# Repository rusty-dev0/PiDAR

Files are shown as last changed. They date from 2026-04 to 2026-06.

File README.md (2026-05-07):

# PiDAR
An autonomous robot that builds a real-time 2D map of an unknown room using LiDAR and SLAM, with live visualization and path tracking, and even a custom development board for all of its locomotive needs!

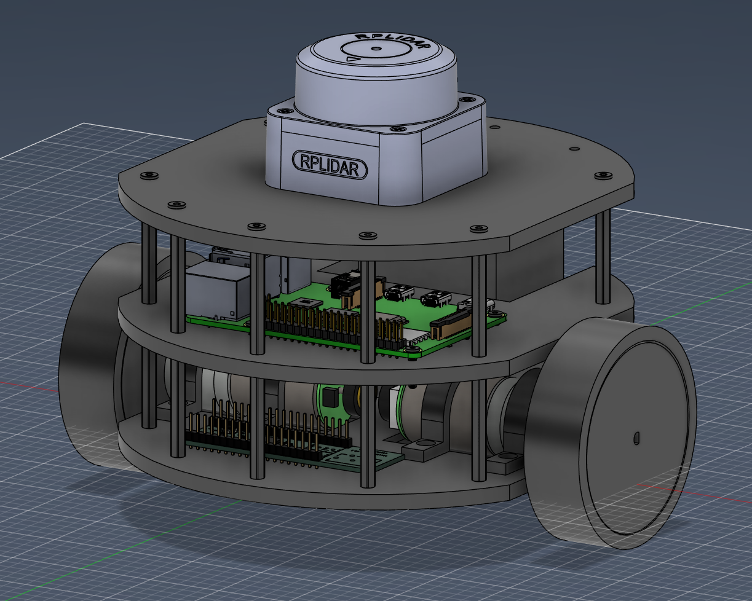
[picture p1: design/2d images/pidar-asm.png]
PiDAR CAD ASMBLY

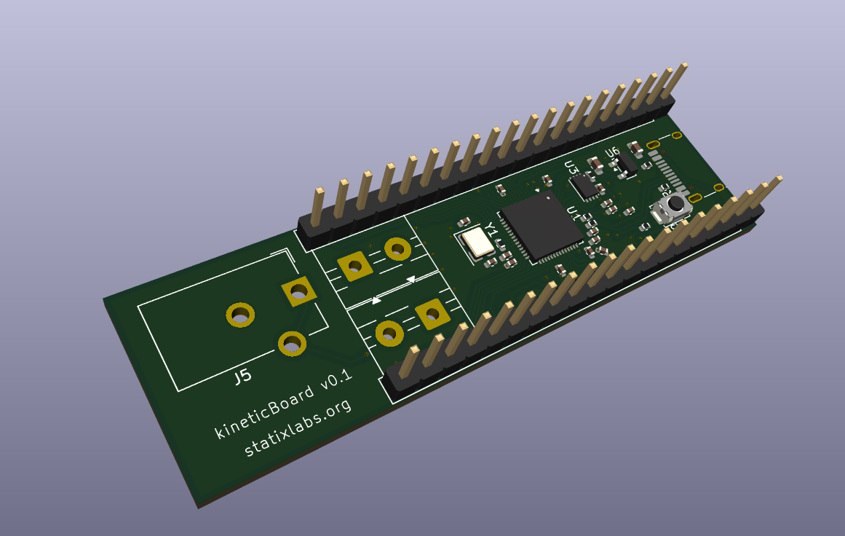
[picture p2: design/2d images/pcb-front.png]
kineticBoard Front

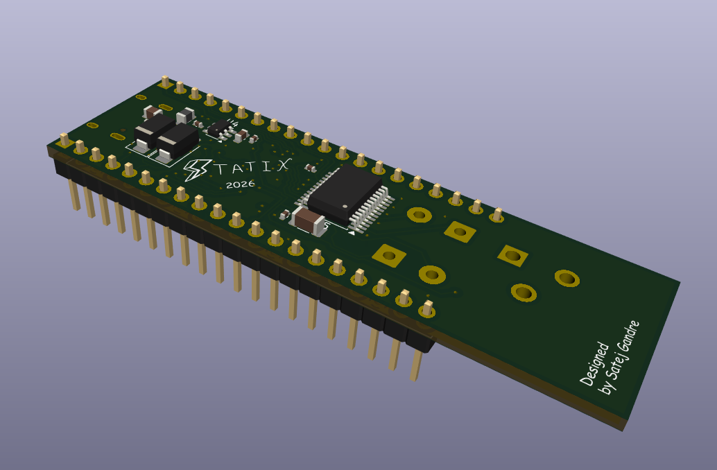
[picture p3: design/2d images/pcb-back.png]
kineticBoard Back


### Programming stuff:

stats

The majority of the code here written for the kineticBoard would be written in the Pico C SDK. This is because abstraction, as seen with MicroPython, often causes delays and doesn't provide full control over the hardware. The Pi would be programmed in Python because it is better for data processing, visualizations, and (potentially) machine learning algorithms.

### A Little Context
I've always wanted to learn more about LiDARs and autonomous vehicles. This project will also serve as one of my projects for the online portion of the *Stasis* Hackathon, a Hack Club event.

## Organization and Flow
This project is basically divided into a few tiny subproblems that each component is designed to tackle. 
1) The LiDAR (at the top) is meant to collect data by sweeping the polar grid and recording ToF data when obstacles are detected (it knows this because its signal would bounce back). The LiDAR then feeds this real-time data to a Raspberry Pi 4 Model B.
2) The Pi, on the layer below, processes the data and allows for stuff like visualizations and algorithms. It's basically the brain of the robot. It takes an input from the layer above, processes it, and then handles an appropriate response such as sending a signal to the kineticBoard or responding to a request on its webserver.
3) The kineticBoard, at the very bottom, connects to the +12V LiPo and handles all of the low-level stuff with the motors. It connects to the encoders and reads the pulses generated by its fluctuating magnetic field, and also drives a response from its built-in TB6612FNG motor driver to the motor terminals themselves, allowing the robot to move forward, backward, spin, etc.

It's kind of like the OSI & TCP/IP model because the abstraction being lowered and lowered with every layer.

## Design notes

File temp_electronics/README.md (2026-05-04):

Stasis won't let me submit KiCAD stuff in a diff repo even though its linked as a submodule so I'm making a temporary copy here, but please check the actual submodule itself.

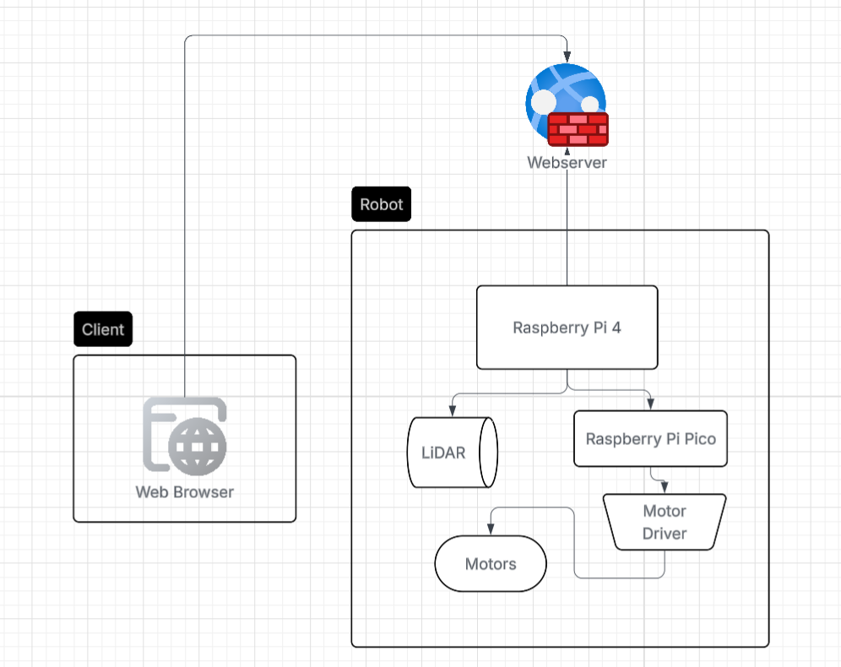
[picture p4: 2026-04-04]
design/2d images/diagram.png

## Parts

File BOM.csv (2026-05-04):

Name | Purpose | Quantity | Total Cost (USD) | Link | Distributor
M3 Standoffs | to hold the different layers of the chasis together | 1 | 6.99 | https://www.amazon.com/Jucoan-Standoffs-Assortment-Threaded-Motherboard/dp/B08DMSNB8X/ref=sr_1_25 | Amazon
Screw Assortment Kit | to hold components into the chasis frame (mainly M2.5 and M3) | 1 | 7.99 | https://www.amazon.com/HanTof-Countersunk-Assortment-Phillips-Threaded/dp/B0FF4RFTN6/ref=sr_1_9 | Amazon
Rechargeable Lithium-Ion Battery Pack | to power the motors independently | 1 | 18.99 | https://www.amazon.com/Zenshynix-Rechargeable-Lithium-Ion-High-Capacity-Telescope/dp/B0G1SW4JHR | Amazon
2Pcs Gear Motor with Encoder | for movement and distance tracking for localization | 1 | 33.29 | https://www.amazon.com/XiaoR-Motor-Encoder-100RPM-Ratio/dp/B0FFMK7CLT | Amazon

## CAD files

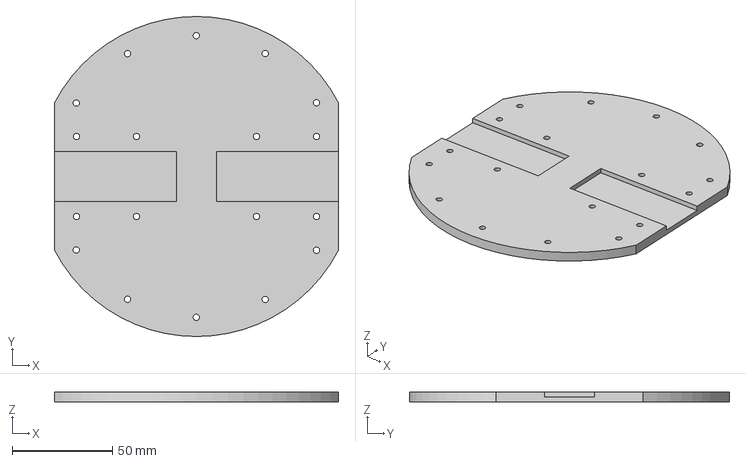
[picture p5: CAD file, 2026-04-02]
design/3d models/step/Chasis.step
142.0 x 160.0 x 5.00 mm

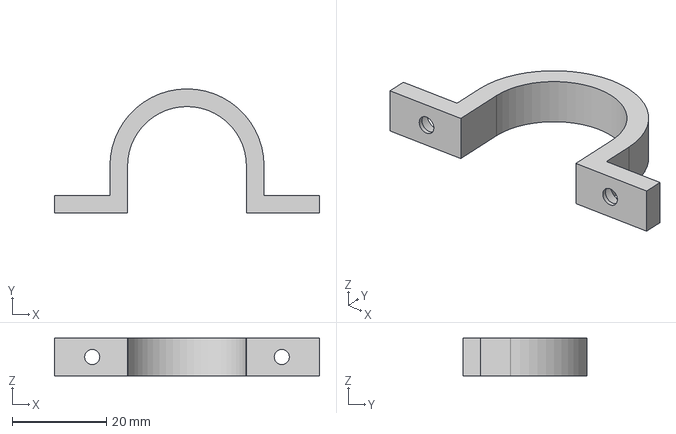
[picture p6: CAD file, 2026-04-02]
design/3d models/step/Saddle Clamp.step
56.2 x 26.4 x 8.00 mm

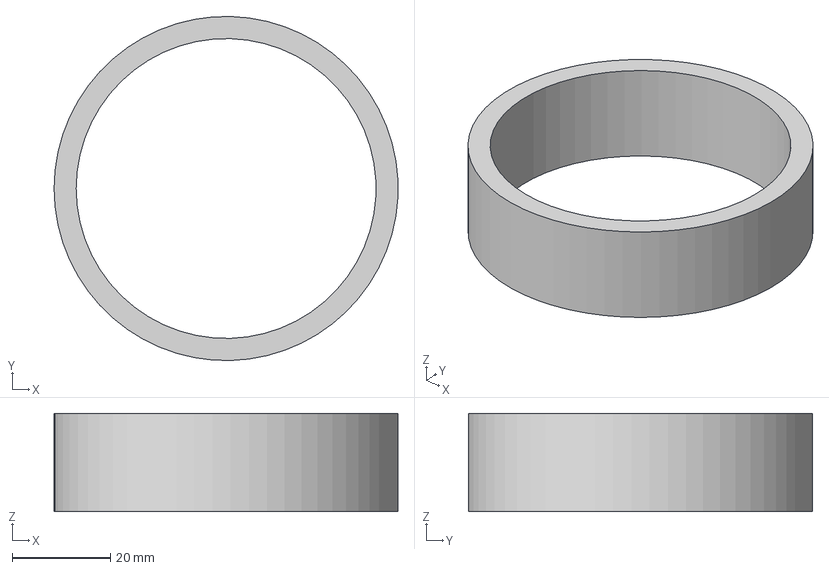
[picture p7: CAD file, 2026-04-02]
design/3d models/step/Tire.step
70.0 x 70.0 x 20.0 mm

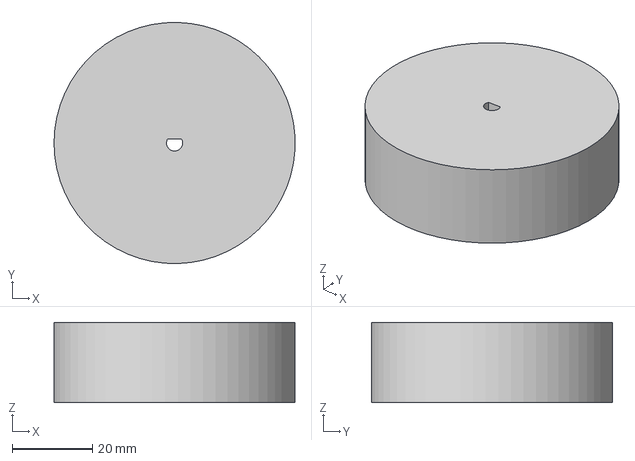
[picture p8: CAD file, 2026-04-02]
design/3d models/step/Wheel.step
60.0 x 60.0 x 20.0 mm

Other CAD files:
design/3d models/step/Middle Chasis.step
design/3d models/step/Upper Chasis.step
design/3d models/Chasis.f3d
design/3d models/Middle Chasis.f3d
design/3d models/Saddle Clamp.f3d
design/3d models/Tire.f3d
design/3d models/Upper Chasis.f3d
design/3d models/Wheel.f3d

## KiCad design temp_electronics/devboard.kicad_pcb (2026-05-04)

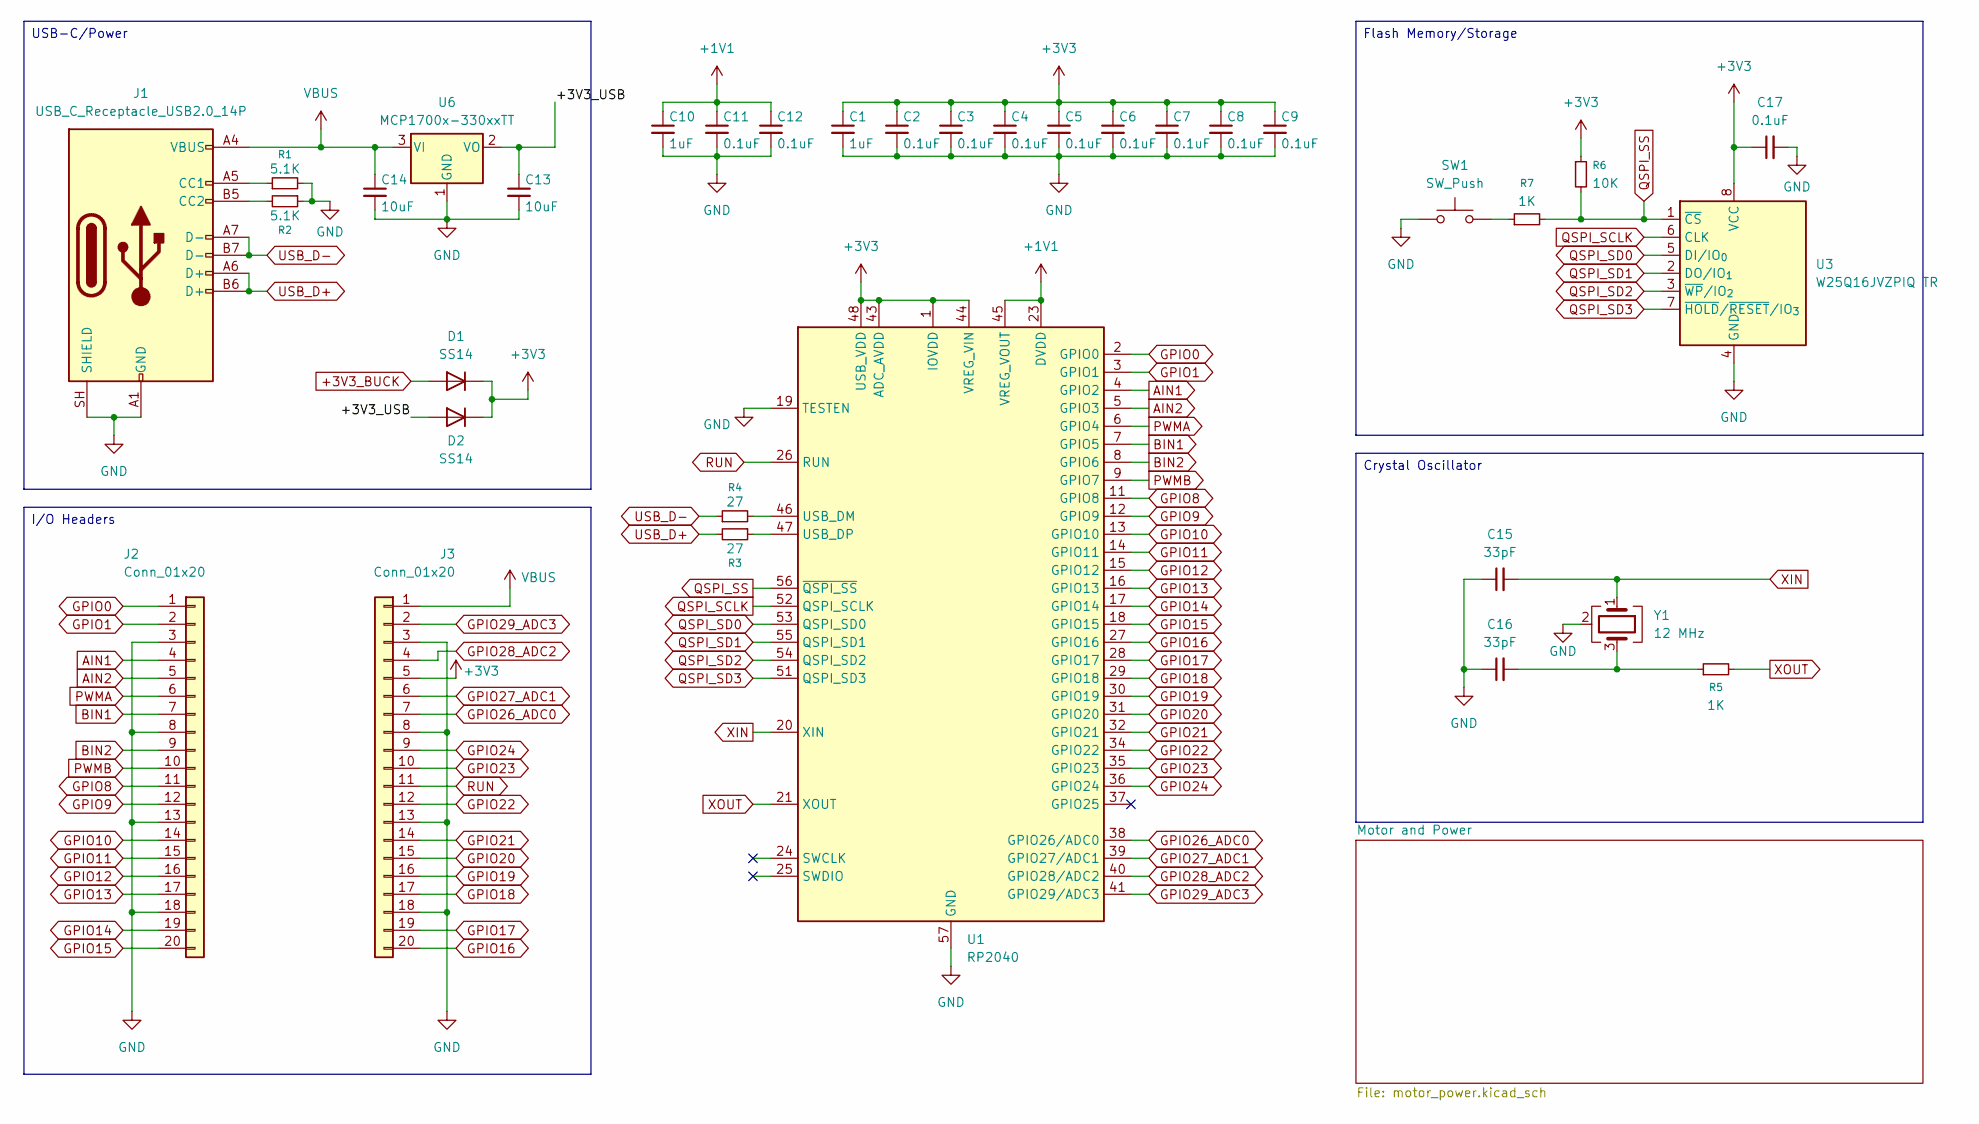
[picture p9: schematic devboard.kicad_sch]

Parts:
C1, C10: 1uF; C_0402_1005Metric
C2, C3, C4, C5, C6, C7, C8, C9, C11, C12, C17: 0.1uF; C_0402_1005Metric
C13, C14: 10uF; C_0603_1608Metric
C15, C16: 33pF; C_0402_1005Metric
D1, D2: SS14; D_SMA
J1: USB_C_Receptacle_USB2.0_14P; USB_C_Receptacle_HRO_TYPE-C-31-M-12
J2, J3: Conn_01x20; PinHeader_1x20_P2.54mm_Vertical
R1, R2: 5.1K; R_0402_1005Metric
R3, R4: 27; R_0402_1005Metric
R5, R7: 1K; R_0402_1005Metric
R6: 10K; R_0402_1005Metric
SW1: SW_Push; SW_Push_SPST_NO_Alps_SKRK
U1: RP2040; QFN-56-1EP_7x7mm_P0.4mm_EP3.2x3.2mm
U3: W25Q16JVZPIQ TR; Winbond_USON-8-1EP_3x2mm_P0.5mm_EP0.2x1.6mm
U6: MCP1700x-330xxTT; SOT-23
Y1: 12 MHz; Crystal_SMD_3225-4Pin_3.2x2.5mm

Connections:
+1V1: C10.1, C11.1, C12.1, U1.23 (DVDD), U1.45 (VREG_VOUT), U1.50 (DVDD)
+3V3: C1.1, C2.1, C3.1, C4.1, C5.1, C6.1, C7.1, C8.1, C9.1, C17.1, D1.1 (K), D2.1 (K), J3.5, R6.1, U1.1 (IOVDD), U1.10 (IOVDD), U1.22 (IOVDD), U1.33 (IOVDD), U1.42 (IOVDD), U1.43 (ADC_AVDD), U1.44 (VREG_VIN), U1.48 (USB_VDD), U1.49 (IOVDD), U3.8 (VCC); also elsewhere on the board
+3V3_BUCK: D1.2 (A); also elsewhere on the board
/+3V3_USB: C13.1, D2.2 (A), U6.2 (VO)
AIN1: J2.4, U1.4 (GPIO2); also elsewhere on the board
AIN2: J2.5, U1.5 (GPIO3); also elsewhere on the board
BIN1: J2.7, U1.7 (GPIO5); also elsewhere on the board
BIN2: J2.9, U1.8 (GPIO6); also elsewhere on the board
GND: C1.2, C2.2, C3.2, C4.2, C5.2, C6.2, C7.2, C8.2, C9.2, C10.2, C11.2, C12.2, C13.2, C14.2, C15.1, C16.1, C17.2, J1.A1 (GND), J1.A12 (GND), J1.B1 (GND), J1.B12 (GND), J1.SH (SHIELD), J2.3, J2.8, J2.13, J2.18, J3.3, J3.8, J3.13, J3.18, R1.2, R2.1, SW1.1, U1.19 (TESTEN), U1.57 (GND), U3.4 (GND), U6.1 (GND), Y1.2 (G), Y1.4 (G); also elsewhere on the board
GPIO0: J2.1, U1.2 (GPIO0)
GPIO1: J2.2, U1.3 (GPIO1)
GPIO8: J2.11, U1.11 (GPIO8)
GPIO9: J2.12, U1.12 (GPIO9)
GPIO10: J2.14, U1.13 (GPIO10)
GPIO11: J2.15, U1.14 (GPIO11)
GPIO12: J2.16, U1.15 (GPIO12)
GPIO13: J2.17, U1.16 (GPIO13)
GPIO14: J2.19, U1.17 (GPIO14)
GPIO15: J2.20, U1.18 (GPIO15)
GPIO16: J3.20, U1.27 (GPIO16)
GPIO17: J3.19, U1.28 (GPIO17)
GPIO18: J3.17, U1.29 (GPIO18)
GPIO19: J3.16, U1.30 (GPIO19)
GPIO20: J3.15, U1.31 (GPIO20)
GPIO21: J3.14, U1.32 (GPIO21)
GPIO22: J3.12, U1.34 (GPIO22)
GPIO23: J3.10, U1.35 (GPIO23)
GPIO24: J3.9, U1.36 (GPIO24)
GPIO26_ADC0: J3.7, U1.38 (GPIO26/ADC0)
GPIO27_ADC1: J3.6, U1.39 (GPIO27/ADC1)
GPIO28_ADC2: J3.4, U1.40 (GPIO28/ADC2)
GPIO29_ADC3: J3.2, U1.41 (GPIO29/ADC3)
unnamed: C16.2, R5.1, Y1.3
unnamed: J1.A5 (CC1), R1.1
unnamed: J1.B5 (CC2), R2.2
unnamed: R7.1, SW1.2
unnamed: R4.2, U1.46 (USB_DM)
unnamed: R3.1, U1.47 (USB_DP)
PWMA: J2.6, U1.6 (GPIO4); also elsewhere on the board
PWMB: J2.10, U1.9 (GPIO7); also elsewhere on the board
QSPI_SCLK: U1.52 (QSPI_SCLK), U3.6 (CLK)
QSPI_SD0: U1.53 (QSPI_SD0), U3.5 (DI/IO_{0})
QSPI_SD1: U1.55 (QSPI_SD1), U3.2 (DO/IO_{1})
QSPI_SD2: U1.54 (QSPI_SD2), U3.3 (~WP/IO_{2})
QSPI_SD3: U1.51 (QSPI_SD3), U3.7 (~HOLD/~RESET/IO_{3})
QSPI_SS: R6.2, R7.2, U1.56 (~QSPI_SS), U3.1 (~CS)
RUN: J3.11, U1.26 (RUN)
USB_D+: J1.A6 (D+), J1.B6 (D+), R3.2
USB_D-: J1.A7 (D-), J1.B7 (D-), R4.1
VBUS: C14.1, J1.A4 (VBUS), J1.A9 (VBUS), J1.B4 (VBUS), J1.B9 (VBUS), J3.1, U6.3 (VI)
XIN: C15.2, U1.20 (XIN), Y1.1
XOUT: R5.2, U1.21 (XOUT)

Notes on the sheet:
Crystal Oscillator
USB-C/Power
Flash Memory/Storage
I/O Headers

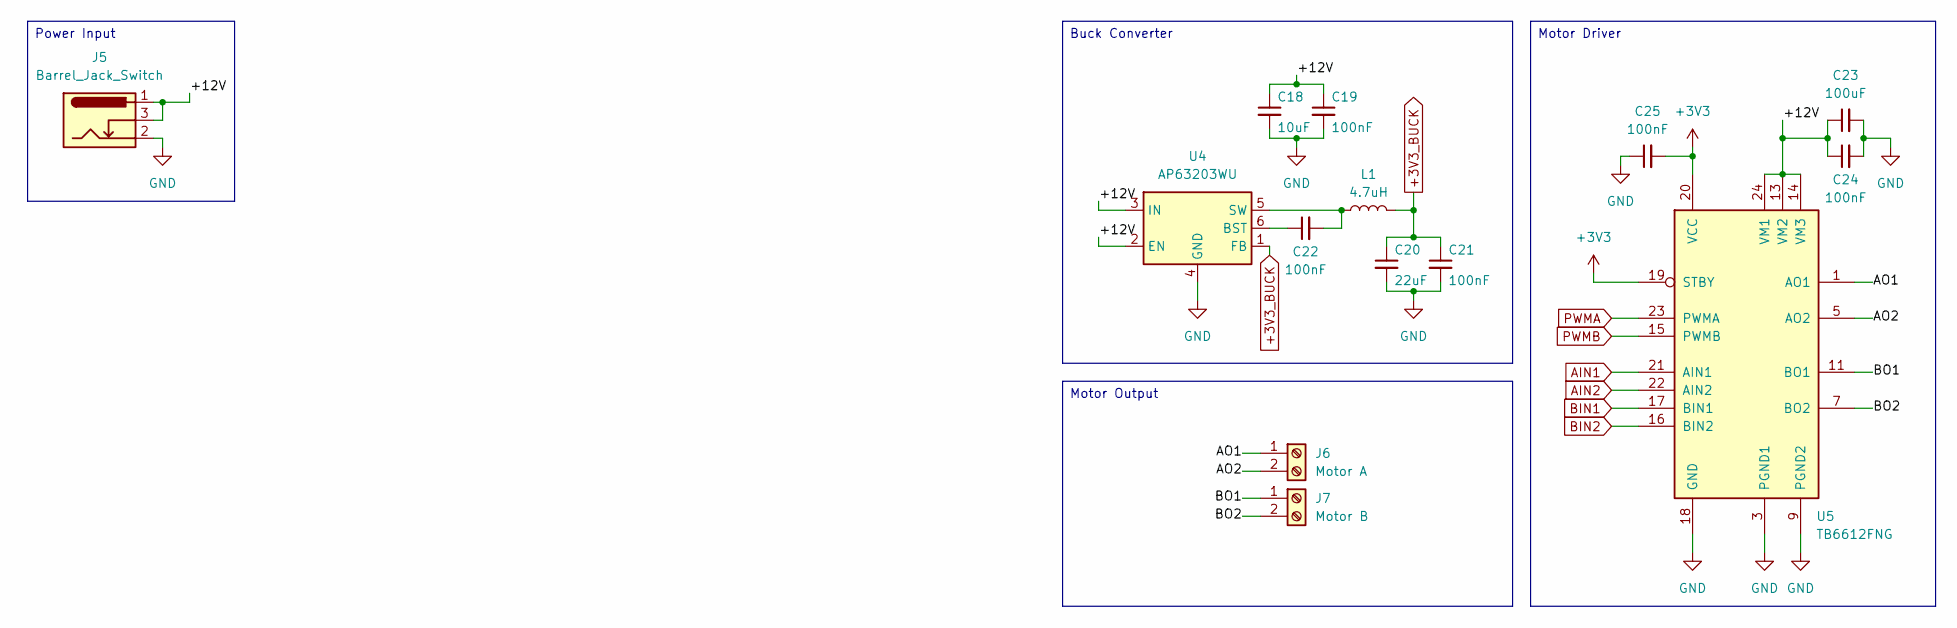
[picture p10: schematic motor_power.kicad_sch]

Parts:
C18: 10uF; C_0603_1608Metric
C19, C21, C22, C24, C25: 100nF; C_0402_1005Metric
C20: 22uF; C_0805_2012Metric
C23: 100uF; C_1206_3216Metric
J5: Barrel_Jack_Switch; BarrelJack_CUI_PJ-102AH_Horizontal
J6: Motor A; TerminalBlock_MaiXu_MX126-5.0-02P_1x02_P5.00mm
J7: Motor B; TerminalBlock_MaiXu_MX126-5.0-02P_1x02_P5.00mm
L1: 4.7uH; L_0805_2012Metric
U4: AP63203WU; TSOT-23-6
U5: TB6612FNG; SSOP-24_5.3x8.2mm_P0.65mm

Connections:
+3V3: C25.2, U5.19 (STBY), U5.20 (VCC); also elsewhere on the board
+3V3_BUCK: C20.1, C21.1, L1.2, U4.1 (FB); also elsewhere on the board
/Motor and Power/+12V: C18.1, C19.1, C23.1, C24.1, J5.1, J5.3, U4.2 (EN), U4.3 (IN), U5.13 (VM2), U5.14 (VM3), U5.24 (VM1)
/Motor and Power/AO1: J6.1, U5.1 (AO1), U5.2 (AO1)
/Motor and Power/AO2: J6.2, U5.5 (AO2), U5.6 (AO2)
/Motor and Power/BO1: J7.1, U5.11 (BO1), U5.12 (BO1)
/Motor and Power/BO2: J7.2, U5.7 (BO2), U5.8 (BO2)
AIN1: U5.21 (AIN1); also elsewhere on the board
AIN2: U5.22 (AIN2); also elsewhere on the board
BIN1: U5.17 (BIN1); also elsewhere on the board
BIN2: U5.16 (BIN2); also elsewhere on the board
GND: C18.2, C19.2, C20.2, C21.2, C23.2, C24.2, C25.1, J5.2, U4.4 (GND), U5.3 (PGND1), U5.4 (PGND1), U5.9 (PGND2), U5.10 (PGND2), U5.18 (GND); also elsewhere on the board
unnamed: C22.1, U4.6 (BST)
unnamed: C22.2, L1.1, U4.5 (SW)
PWMA: U5.23 (PWMA); also elsewhere on the board
PWMB: U5.15 (PWMB); also elsewhere on the board

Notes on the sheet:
Motor Output
Power Input
Buck Converter
Motor Driver

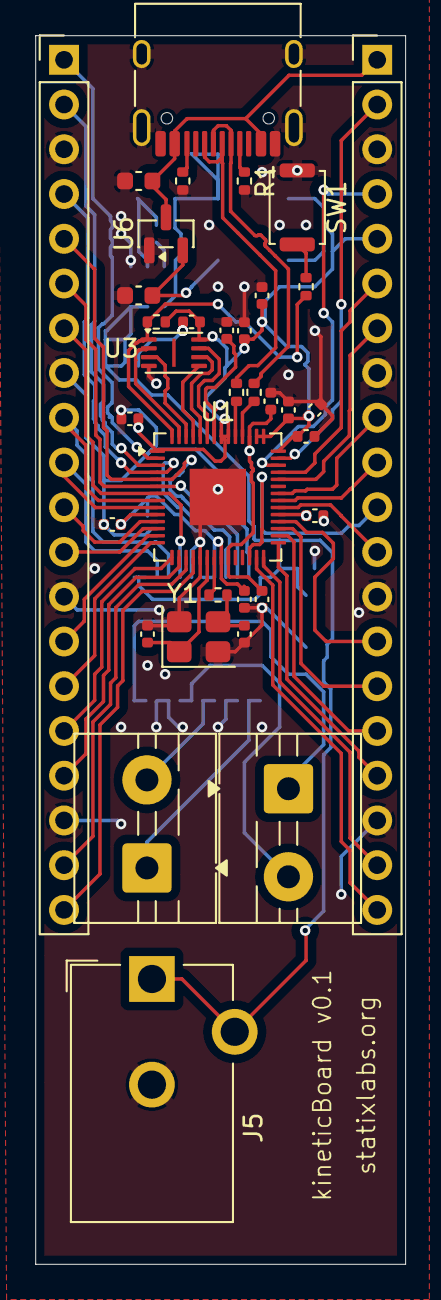
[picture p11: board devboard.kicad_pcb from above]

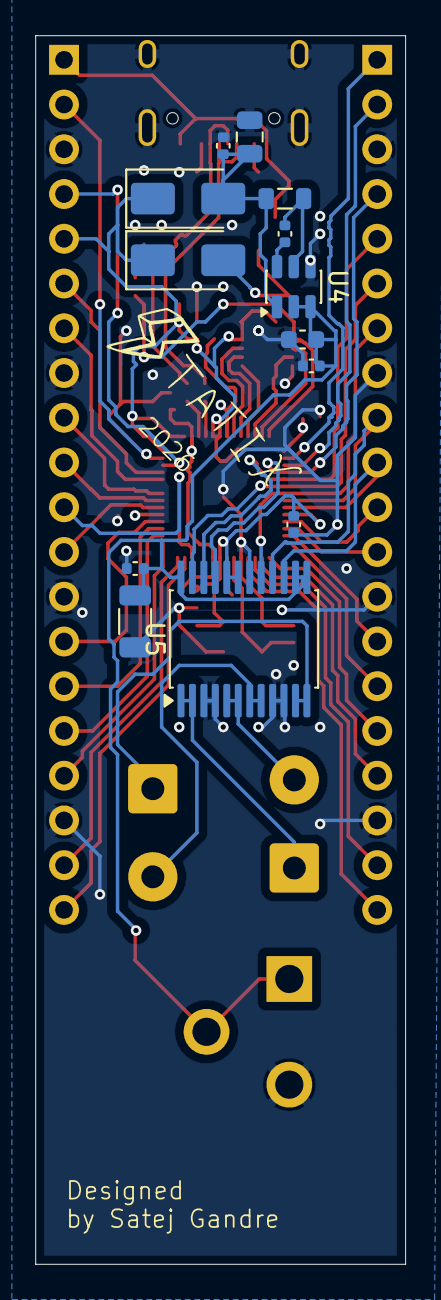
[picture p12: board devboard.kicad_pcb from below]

Board: 4 copper layers, 21.0 x 69.8 mm, 48 parts (13 on the bottom side), 59 nets.

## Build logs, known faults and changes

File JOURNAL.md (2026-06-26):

<!--
  This journal is auto generated by Stasis.
-->

# 5/3/2026 7 PM - completed CAD assembly!

_Time spent: 1.75h_

Okay, I have to admit, this part of the project was really cool and intuitive.

I imported a [Raspberry Pi 4 Model B](https://grabcad.com/library/raspberry-pi-4-model-b-1) model from the internet as well as a model for the [RPLiDAR C1](https://grabcad.com/library/rplidar-c1-1) and the [motors](https://grabcad.com/library/polulu-25d-metal-gear-motor-configurable-1), which I forgot to cite in my prior entry. I manually made a simple component for the battery pack (its just a rect. prism lol).

Since I didn't consider how the Raspberry Pi would be powered in my earlier diagrams, I settled on squeezing in a slim 6 mm powerbank vertically in between the 12V LiPo and the chasis cutoffs.

It was annoying that the RPi and the LiDAR use 2.5M screws while the rest of my design uses 3M but oh well we'll just stick with it. Another annoying thing was adding the nuts on the back of a surface, because it was hard to see if the screw would perfectly align.

Overall, assembling everything was quite intuitive and I enjoyed doing it! (I'm sticking with those default tires because I'm not running this on carpet). I ordered some TPU (95A) to 3D print this with next week.

Here's the final assembly:


...and the bottom view:





# 5/3/2026 3 AM - started working on the final CAD assembly

_Time spent: 2h_

I started working on combining all of the parts into a single assembly, which is actually kinda complex, but it felt good working with Fusion again after a whole month of KiCAD.

I first had to find some premade 3D designs for the motor and the Raspberry Pi (NOT the kineticBoard; I extraced the 3D files from that in KiCAD). This took a while since for some reason the only quality motors I found online were of 37d and I'm looking for 25d.

I then started inserting the individual components in the assembly, starting with the base chasis, the clamps, the motors, and then the screws. Instead of fasteners, I decided to go the easy route and use the McMaster-Carr menu for M3 screws. I also was tasked to finally figure out a way in which I'm supposed to stack the boards, so I decided to have standoffs support each layer, and the middle layer won't have screws, but rather threaded rods.

I still need to figure out a 3D model for the battery (which is why you see three holes that don't have a standoff), but I think I can get away with something simple like a rectangular prism if I can't find anything else online.

Here is how it looks so far (I'm pretty much done with the first layer only; future layers will stack):








# 5/2/2026 10 PM - finished the kineticBoard!

_Time spent: 6.5h_

I've basically been stuck for the entire week, but today I gained momentum and finished up this board.

I was having SO MANY issues with routing. First of all, since it was my first time using KiCAD, the differential pair stuff was being weird and it took me 2 days of no progress just to figure out how to tune the lengths properly because for some reason selecting the D+ trace for example and clicking again didn't do anything. I still don't know what I did to get it to work, but whatever it did seemed to reduce the error to like 1E-5 so that should be good.

But that was the easy part lol. The actual difficulty resided in the routing itself. At first, I was using a 2 layer board and adding traces felt easy. The only rules I had to follow were to not have right-angle bends and try not to put via's on pads...and then all the games came to an end after the PCB was half full. All of a sudden, I actually had to route things with space and efficiency in mind, and I couldn't just place traces wherever I wanted. Since I kind of screwed up already, I had to painfully rewire my prior traces. Somehow, I managed to get both layers of the PCB done after many hours of frustration.

And then came the copper fill zone. I thought this would be super simple as all I had to do was outline a zone and press [B] and let the magic happen...yeah, no. It ended up being so stupid that I had to create random via's wherever islands popped up, and sometimes the GND header pins themselves were isolated from the other parts of my board, and fixing those was an even larger headache because there were a billion traces that blocked traces leaving the header pins. After a lot of contemplation, I decided to just use a 4 layer PCB and drop via's (which btw didn't place exactly where I wanted to) in the green layer and handle stuff in that. I literally needed "out of the box" wiring😭.

Eventually, I perserved and finished the whole routing stuff with the help of the push and shove mode (bless whoever made that). I added some finishing touches to my design like a logo for Statix (which is a nonprofit where I plan to document this board somewhere after the hackathon) and some personal stuff like my name.

Overall, this was a pretty exhausting yet fun experience, and my respect towards the people who design these has increased tenfold. Despite being stuck for hours and frantically watching outdated guides on YouTube, I learned a lot from this design and I feel way more confident with my engineering skills.

Here are some pics of the final design:











# 4/22/2026 3 AM - finished secondary schematic and began working on the PCB

_Time spent: 5.25h_

I decided to combine a motor driver, the `TB6612FNG`, with my breadboard. This might sound pretty dumb because anyone could just connect the two components on a breadboard, but I don't have the space for that on my limited chasis. 

Before editing the schematic, I had to research into the specifics of the `TB6612FNG` as well as find out how to power the board with a 12V supply. I ended up having to go down a rabbit hole of buck converters but found one simple enough: the `AP63203WU-7`. This needed a 4.7uH inductor to smoothen it out to a steady 3.3V, in addition to more decoupling capacitors.

I decided to create a secondary hierarchical sheet and implement the new power systems and motor driver there. I connected a +12V net label to a barrel jack sized for the 2.1mm x 5.5mm plug on my battery pack, and ran that same rail into the buck converter input. The buck output feeds into a diode OR-ing circuit alongside the existing `MCP1700x-330xxTT` from the USB-C section, so the board powers itself from whichever source is available without any manual switching.



The `TB6612FNG` sits on the same sheet, with its VM motor supply rail drawing directly from the 12V barrel jack and its logic VCC pulling from the 3.3V rail. All 7 control signals --- AIN1, AIN2, BIN1, BIN2, PWMA, PWMB, and STBY --- are wired to GPIO2 through GPIO8 on the RP2040 via global labels crossing between schematic sheets. Motor outputs connect to two screw terminals for easy wiring to whatever motors end up on the chassis.





I also began placing the components in their respective places in the PCB editor. One issue that I'm currently facing is the 3-pin debug connector appears to be larger the one in the guide, despite having the exact same name for the footprint.

Overall, I spent a lot of time researching and finding out which components to place, since this is my first time making a PCB on my own without following a tutorial.








# 4/19/2026 1 AM - began working on a devboard featuring an integrated motor driver

_Time spent: 4h_

To meet the complexity requirements (and also to learn more stuff in embedded systems), I decided to create my own devboard that has a built-in motor driver rather than using a breadboard and manually wiring up the a Raspberry Pi Pico to, idk, suppose a TB6612FNG.

I opened KiCAD for the first time and read through the first half of this guide on how to build a custom devboard (based on the RP2040).

While reading the guide, I learned how stuff from my Physics: E&M course relates to real-world electronics. This tiny schematic also finally taught me how the Pico --- a tool which I've been using for 3+ years --- actually works. Who knew that the flash memory/storage chip uses QSPI, or that clock signals are given by crystal oscillators? I also learned how BOOTSEL enables CS pin of the aforementioned QSPI channel, which really blew my mind and made my understanding of the Pico feel more complete.

I ran into a few issues with directionallity with global labels. There isn't an option that I see on the toolbar for it, so for anyone reading this using version 10.0, the shortcut `Ctrl + L` is guaranteed to work.

After finishing the schematic, I set up a seperate GitHub repo and added it to the mainstream one as a submodule. This is because I really like the idea of making a custom devboard, and I'd like to take it further even after this hackathon ends.

Overall, I felt like this was a wonderful introduction to PCB CAD software and made me reflect and truly understand some of the stuff that I've been using since middle school.

Here's a picture of my inital schematic:

kicad-result-1

P.S. I'm naming the custom devboard "[kinetic](https://github.com/rusty-dev0/kinetic)" because it provides movement to whatever its connected to.



# 4/4/2026 4 AM - Finished Chasis Design

_Time spent: 4h_

Really just the title lol.

I created copies of my initial chasis baseplate and modified it. I ran into like a dozen issues with the initial design and had to rework the next layers since the battery pack would shift the robot's center of mass to a concerningly distant spot. I'm just hoping I can even out the distribution by using velcro to attach a portable charger to the other side of the chasis below the wheels.

Additionally, I read through some sketchy documentation and gabmled away between what Google AI overview was saying vs what SLAMTEC (the company that made the LiDAR I'll be using) said about distances between M3 screw holes. Hopefully its 43 mm (fingers crossed!!).

I also had to update the parts list for a kit that contained not just M3 screws because both SLAMTEC and Raspberry Pi decided to be special by using M2.5 screws out of nowhere.

I'm planning on being lazy by stacking standoffs to create the vertical backbone that keeps this thing together cuz I really don't feel like threading anything in Fusion.

Anyway, this design stuff is turning to look into something actually managable lol.








# 4/3/2026 12 AM - Setup and Initial Chasis Design

_Time spent: 6h_

Hey there,

I'm Satej.

I guess this marks the beginning of my PiDAR project.

I did a few things this session:
* 1. Set up the GitHub and created a small readme
* 2. Created an architecture diagram in Lucid to map out how different devices will interface with one another
* 3. Tried to develop a chasis in Tinkercad but realized its not precise enough for the build I'm doing.
* 4. Used Fusion to create the model instead! (This took the most time!!!)

I was genuinely gonna use Tinkercad for this entire build because I was too afraid to learn Fusion. Apparently, it only takes an hour or two to get used to it lol.

I was stuck on the chasis for like a solid 3 hours, but it was so worth it. This was partially because I was using it for the first time and made so many mistakes, but in the end, I got used to it and was able to create a clamp and a wheel + tire without searching a billion things up on Google!

So the CAD stuff I did today was mainly for the lower chasis. I plan to have the Pi Pico at this level alongside its motor driver components and breadboard. I'll prolly have to squeeze in room for a power supply somewhere too.

The upper chasis --- which I havent worked on yet --- is gonna contain the RPLiDAR and a regular Pi. The Pi will most likely be below the chasis somewhere since I don't want anything obstructing the LiDAR's 2D scan.

Btw, I exported .f3d and .step files and put them in the `/design/3d models/` and `/design/3d models/step` directories, respectively.

Here are some pictures of the models and diagrams:

WIN_20260402_20_07_48_Pro

WIN_20260402_20_08_56_Pro







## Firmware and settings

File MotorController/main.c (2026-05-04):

#include <stdio.h>
#include "pico/stdlib.h"
#include "TB6612FNG.h"

#define LEFT_IN1   2
#define LEFT_IN2   3
#define LEFT_PWM   4
#define RIGHT_IN1  5
#define RIGHT_IN2  6
#define RIGHT_PWM  7

DualMotorDriver* setup()
{
    stdio_init_all();

    printf("[in setup()] setting up motor controller\n");

    DualMotorDriver controller;
    tb6612fnd_init(&controller, LEFT_IN1, LEFT_IN2, LEFT_PWM, RIGHT_IN1, RIGHT_IN2, RIGHT_PWM);

    printf("[in setup()] motor controller sucessfully initialized\n");
    return &controller;
}

int main()
{
    DualMotorDriver* controller = setup();

    while (1)
    {
        printf("[in main()] moving forward\n");
        tb6612fng_forward(controller, 32768);
        sleep_ms(2000);

        printf("[in main()] moving backward\n");
        tb6612fng_backward(controller, 32768);
        sleep_ms(2000);

        printf("[in main()] turning left\n");
        tb6612fng_turn_left(controller, 32768);
        sleep_ms(2000);

        printf("[in main()] turning right\n");
        tb6612fng_turn_right(controller, 32768);
        sleep_ms(2000);

        printf("[in main()] stopping\n");
        tb6612fng_stop(controller);
        sleep_ms(2000);
    }

}

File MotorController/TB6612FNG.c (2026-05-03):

#include "TB6612FNG.h"
#include "hardware/pwm.h"
#include "hardware/gpio.h"
#include "pico/stdlib.h"

static void _configure_motor(Motor *motor) {
    gpio_init(motor->pins.in1);
    gpio_set_dir(motor->pins.in1, GPIO_OUT);
    gpio_init(motor->pins.in2);
    gpio_set_dir(motor->pins.in2, GPIO_OUT);

    gpio_set_function(motor->pins.pwm, GPIO_FUNC_PWM);
    motor->pwm_slice = pwm_gpio_to_slice_num(motor->pins.pwm);
    motor->pwm_channel = pwm_gpio_to_channel(motor->pins.pwm);

    pwm_config config = pwm_get_default_config();
    pwm_config_set_clkdiv(&config, 125.0f);
    pwm_config_set_wrap(&config, 65535);
    pwm_init(motor->pwm_slice, &config, true);
    motor->max_pwm = 65535;
}

void tb6612fng_init(DualMotorDriver *driver, uint8_t left_in1, uint8_t left_in2, uint8_t left_pwm, uint8_t right_in1, uint8_t right_in2, uint8_t right_pwm) {
    driver->left_motor.pins.in1 = left_in1;
    driver->left_motor.pins.in2 = left_in2;
    driver->left_motor.pins.pwm = left_pwm;
    _configure_motor(&driver->left_motor);

    driver->right_motor.pins.in1 = right_in1;
    driver->right_motor.pins.in2 = right_in2;
    driver->right_motor.pins.pwm = right_pwm;
    _configure_motor(&driver->right_motor);

    tb6612fng_stop(driver);
}

void tb6612fng_set_motor(Motor *motor, MotorDirection direction, MotorSpeed speed) {
    switch (direction) {
        case MOTOR_FORWARD:
            gpio_put(motor->pins.in1, 1);
            gpio_put(motor->pins.in2, 0);
            break;
        case MOTOR_BACKWARD:
            gpio_put(motor->pins.in1, 0);
            gpio_put(motor->pins.in2, 1);
            break;
        case MOTOR_STOP:
            gpio_put(motor->pins.in1, 0);
            gpio_put(motor->pins.in2, 0);
            break;
    }

    pwm_set_chan_level(motor->pwm_slice, motor->pwm_channel, speed);
}

void tb6612fng_forward(DualMotorDriver *driver, MotorSpeed speed) {
    tb6612fng_set_motor(&driver->left_motor, MOTOR_FORWARD, speed);
    tb6612fng_set_motor(&driver->right_motor, MOTOR_FORWARD, speed);
}

void tb6612fng_backward(DualMotorDriver *driver, MotorSpeed speed) {
    tb6612fng_set_motor(&driver->left_motor, MOTOR_BACKWARD, speed);
    tb6612fng_set_motor(&driver->right_motor, MOTOR_BACKWARD, speed);
}

void tb6612fng_turn_left(DualMotorDriver *driver, MotorSpeed speed) {
    tb6612fng_set_motor(&driver->left_motor, MOTOR_FORWARD, speed / 2);
    tb6612fng_set_motor(&driver->right_motor, MOTOR_FORWARD, speed);
}

void tb6612fng_turn_right(DualMotorDriver *driver, MotorSpeed speed) {
    tb6612fng_set_motor(&driver->left_motor, MOTOR_FORWARD, speed);
    tb6612fng_set_motor(&driver->right_motor, MOTOR_FORWARD, speed / 2);
}

void tb6612fng_rotate_left(DualMotorDriver *driver, MotorSpeed speed) {
    tb6612fng_set_motor(&driver->left_motor, MOTOR_BACKWARD, speed);
    tb6612fng_set_motor(&driver->right_motor, MOTOR_FORWARD, speed);
}

void tb6612fng_rotate_right(DualMotorDriver *driver, MotorSpeed speed) {
    tb6612fng_set_motor(&driver->left_motor, MOTOR_FORWARD, speed);
    tb6612fng_set_motor(&driver->right_motor, MOTOR_BACKWARD, speed);
}

void tb6612fng_stop(DualMotorDriver *driver) {
    tb6612fng_set_motor(&driver->left_motor, MOTOR_STOP, 0);
    tb6612fng_set_motor(&driver->right_motor, MOTOR_STOP, 0);
}

void tb6612fng_set_speed(DualMotorDriver *driver, MotorSpeed left_speed, MotorSpeed right_speed) {
    pwm_set_chan_level(driver->left_motor.pwm_slice, driver->left_motor.pwm_channel, left_speed);
    pwm_set_chan_level(driver->right_motor.pwm_slice, driver->right_motor.pwm_channel, right_speed);
}

int linearly_map(int x, int in_min, int in_max, int out_min, int out_max) {
    return (x - in_min) / (in_max - in_min) * (out_max - out_min)  + out_min;
}

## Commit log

2026-04-02 added lower portion of the robot chasis
    [Chasis.f3d, Chasis.step, Saddle Clamp.f3d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]
2026-04-02 sketched out a diagram in Lucid and updated readme
    [Chasis.f3d, Chasis.step, Saddle Clamp.f3d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]
2026-04-04 finished chasis design (hopefully)
    [Middle Chasis.f3d, Middle Chasis.step, Upper Chasis.f3d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]
2026-04-04 finished chasis f3d
    [Middle Chasis.f3d, Upper Chasis.f3d]
2026-04-04 added step variants of finished chasis plates
    [Middle Chasis.step, Upper Chasis.step]
2026-04-04 added files back??
    [Middle Chasis.f3d, Middle Chasis.step, Upper Chasis.f3d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]
2026-04-21 updated kinetic board
2026-04-22 pcb update
2026-05-02 updated to the finished board
2026-05-03 completed assembly
2026-05-04 added BOM
    [BOM.csv]
2026-05-04 copied submodule content in current repo to pass stasis autochecks
    [devboard.kicad_pcb, devboard.kicad_sch, freerouting.dsn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]
